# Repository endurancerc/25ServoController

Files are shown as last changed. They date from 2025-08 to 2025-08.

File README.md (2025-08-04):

# 25 Servo Controller

Build your own 25 Servo Controller! Once you have your circuit you must flash the bootloader firmware to your 
  device. Upload device firmware using the PICDEM tool.
  
The commercial version can be found here:

[http://www.endurance-rc.com/controllers.php#tfservo](http://www.endurance-rc.com/controllers.php#tfservo)

Requires Device Circuit.

-------------------------------------------------------------------------------------------------------------------------

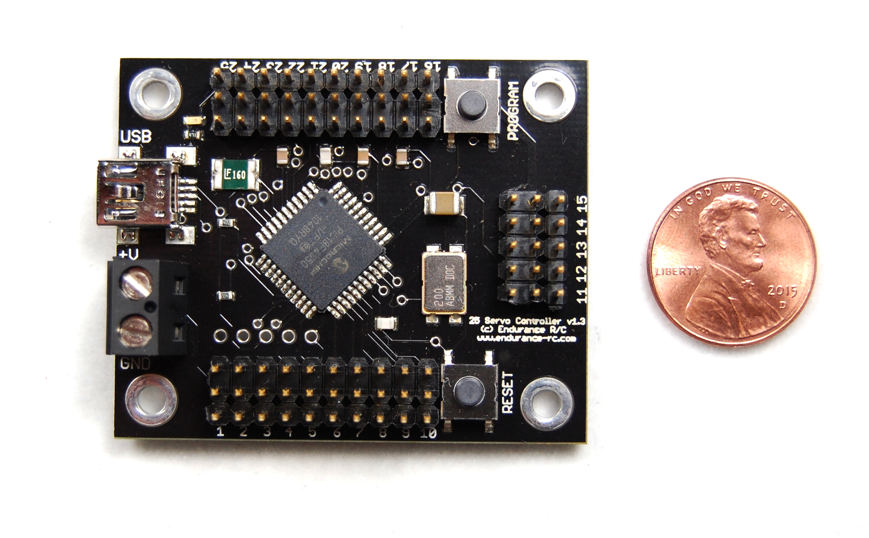
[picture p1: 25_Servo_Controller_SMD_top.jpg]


[25 Servo Controller Bill of Materials](https://github.com/endurancerc/PIC18F4550-25ServoController/blob/main/25_Servo_Controller_BOM.csv)

[25 Servo Controller Instructions](https://github.com/endurancerc/PIC18F4550-25ServoController/blob/main/25_servo_controller_v1.2_instructions.pdf)

-------------------------------------------------------------------------------------------------------------------------
        ______          __                                    ____     ________
       / ____/___  ____/ /_  ___________ _____  ________     / __ \  _/_/ ____/
      / __/ / __ \/ __  / / / / ___/ __ `/ __ \/ ___/ _ \   / /_/ /_/_// /     
     / /___/ / / / /_/ / /_/ / /  / /_/ / / / / /__/  __/  / _, _//_/ / /___   
    /_____/_/ /_/\__,_/\__,_/_/   \__,_/_/ /_/\___/\___/  /_/ /_/_/   \____/   

-------------------------------------------------------------------------------------------------------------------------

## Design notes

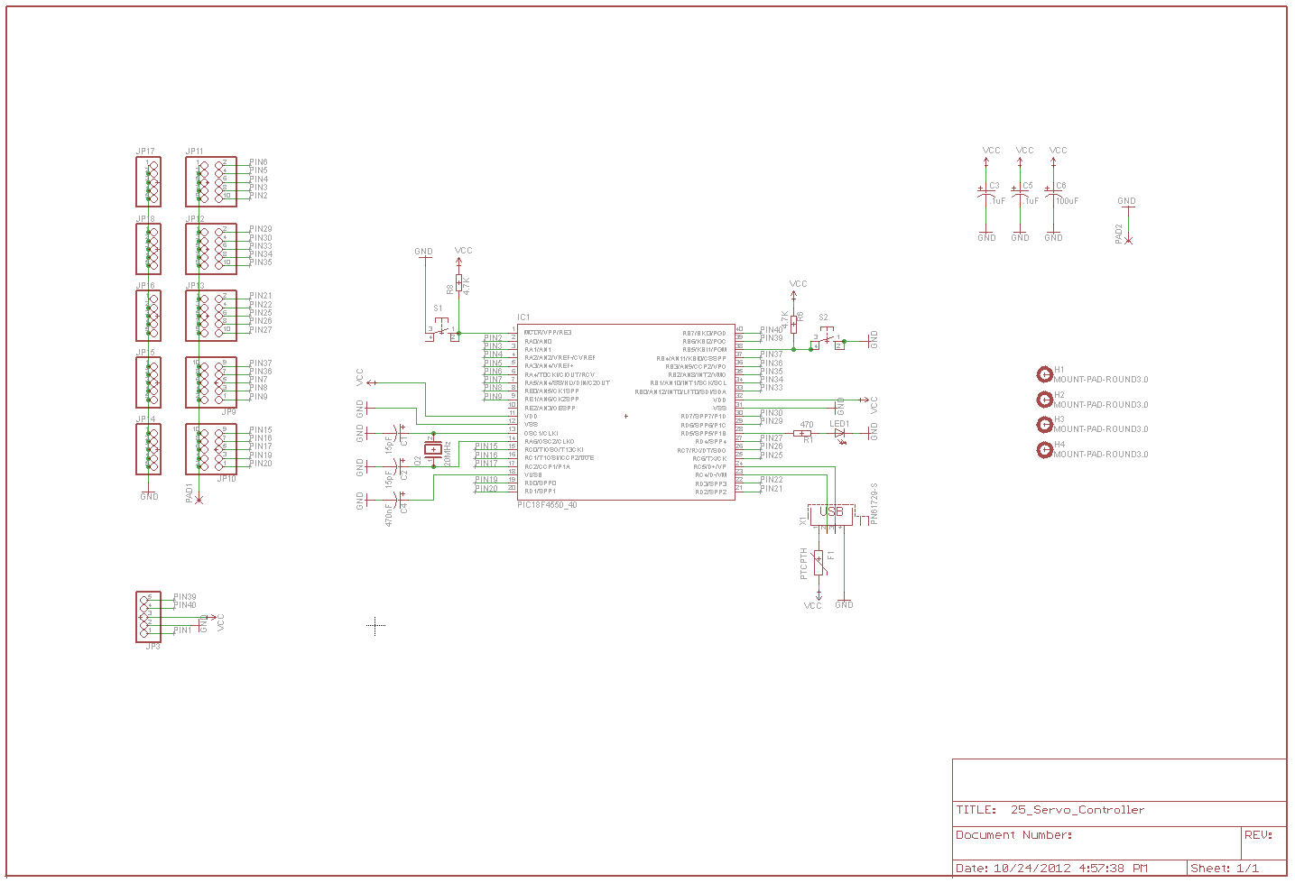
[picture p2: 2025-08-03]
Circuit_Board/25_Servo_Controller_Schematic.jpg

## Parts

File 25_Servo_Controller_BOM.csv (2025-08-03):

25 Servo Controller Parts Listing
Schematic Part ID | Mouser Part Number | Manufacturer Part Number | Description
IC1 | 579-PIC18F4550-I/P | PIC18F4550-I/P | Microcontrollers (MCU) 32kBF 2048RM FSUSB2
IC1 | 517-4840-6000-CP | 4840-6000-CP | IC & Component Sockets 40P DUAL WIPE DIPSKT
R6 | 291-4.7K-RC | 291-4.7K-RC | Carbon Film Resistors - Through Hole 4.7Kohms 0.05
R8 | 291-4.7K-RC | 291-4.7K-RC | Carbon Film Resistors - Through Hole 4.7Kohms 0.05
S1 | 653-B3F-1000 | B3F-1000 | Tactile & Jog Switches 6X6 FLAT 4.3mm BTN
S2 | 653-B3F-1000 | B3F-1000 | Tactile & Jog Switches 6X6 FLAT 4.3mm BTN
F1 | 576-30R160UPR | 30R160UPR | PTC Resettable Fuses 30V RADIAL LDS 1.60A RADIAL LEADS
Q2 | 815-ABL-20-B2 | ABL-20.000MHZ-B2 | Crystals +/-20ppm 20MHZ FUNDAMENTAL
C1 | 581-SR211A150KAR | SR211A150KAR | Multilayer Ceramic Capacitors (MLCC) - Leaded 100volts 15pF 10% C0G
C2 | 581-SR211A150KAR | SR211A150KAR | Multilayer Ceramic Capacitors (MLCC) - Leaded 100volts 15pF 10% C0G
C3 | 80-C410C104M5U | C410C104M5U5TA | Multilayer Ceramic Capacitors (MLCC) - Leaded 50volts .1uF 20%
C5 | 80-C410C104M5U | C410C104M5U5TA | Multilayer Ceramic Capacitors (MLCC) - Leaded 50volts .1uF 20%
C6 | 647-UVR1J101MPD1TD | UVR1J101MPD1TD | Aluminum Electrolytic Capacitors - Leaded 63volts 100uF
C4 | 140-SEA0R47M1HBK0407 | SEA0R47M1HBK-0407P | Aluminum Electrolytic Capacitors - Leaded 50V 0.47uF 20% 4X7mm
R1 | 660-MF1/4DC4700F | MF1/4DC4700F | Metal Film Resistors - Through Hole 470ohm 1% 100PPM
X1 | 571-292304-1 | 292304-1 | USB Connectors 4P 'B' RECEPTACLE
LED1 | 604-WP7113QBC/D | WP7113QBC/D | Standard LED - Through Hole BLUE WATER CLEAR
JP9-JP13 | 517-2350-6121TG | 2350-6121TG | Headers & Wire Housings 5P STRT 2 ROW GOLD
JP14-JP18 | 517-6111TG | 2340-6111TG | Headers & Wire Housings 5P STRT 1 ROW GOLD
PAD1/PAD2 | 538-39880-0302 | 39880-0302 | Fixed Terminal Blocks 2 CKT TERM. BLOCK 5.08mm
JP3 |  |  | ICSP: 1 - MCLR 2 - GND 3 - +5V 4 - PGD 5 - PGC

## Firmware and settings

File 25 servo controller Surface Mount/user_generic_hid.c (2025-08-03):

/** I N C L U D E S **********************************************************/
#include <p18cxxx.h>
#include <usart.h>
#include <delays.h>
#include "typedefs.h"
#include "usb.h"
#include "io_cfg.h"             // I/O pin mapping
#include "user_generic_hid.h"

/** V A R I A B L E S ********************************************************/
#pragma udata

byte number_of_bytes_read;
char transmit_buffer[EP0_BUFF_SIZE];
char receive_buffer[EP0_BUFF_SIZE];

int count;
unsigned int pulse1, pulse2, pulse3, pulse4, pulse5, pulse6, pulse7, pulse8;
unsigned int pulse9, pulse10, pulse11, pulse12, pulse13, pulse14, pulse15, pulse16;
unsigned int pulse17, pulse18, pulse19, pulse20, pulse21, pulse22, pulse23, pulse24, pulse25;

unsigned int dif1, dif2, dif3, dif4, dif5, dif6, dif7, dif8;
unsigned int dif9, dif10, dif11, dif12, dif13;

/** P R I V A T E  P R O T O T Y P E S ***************************************/
void BlinkUSBStatus(void);
void ReportLoopback(void);
void HandleControlOutReport(void);
void step(int);

/** D E C L A R A T I O N S **************************************************/
#pragma code
void UserInit(void) {

	//PWM Pins
	TRISDbits.TRISD2 = 0; //pin d2 output, output 1
	TRISDbits.TRISD3 = 0; //pin d3 output, output 2
	TRISCbits.TRISC6 = 0; //pin c6 output, output 3
	//TRISCbits.TRISC7 = 0; //pin c7 output, output 4
	TRISDbits.TRISD4 = 0; //pin d4 output, output 5
	TRISDbits.TRISD6 = 0; //pin d6 output, output 6
	TRISDbits.TRISD7 = 0; //pin d7 output, output 7
	TRISBbits.TRISB0 = 0; //pin b0 output, output 8
	TRISBbits.TRISB1 = 0; //pin b1 output, output 9
	TRISBbits.TRISB2 = 0; //pin b2 output, output 10
	TRISAbits.TRISA4 = 0; //pin a4 output, output 11
	TRISAbits.TRISA3 = 0; //pin a3 output, output 12
	TRISAbits.TRISA2 = 0; //pin a2 output, output 13
	TRISAbits.TRISA1 = 0; //pin a1 output, output 14
	TRISAbits.TRISA0 = 0; //pin a0 output, output 15
	TRISBbits.TRISB4 = 0; //pin b4 output, output 16
	TRISBbits.TRISB3 = 0; //pin b3 output, output 17
	TRISAbits.TRISA5 = 0; //pin a5 output, output 18
	TRISEbits.TRISE0 = 0; //pin e0 output, output 19
	TRISEbits.TRISE1 = 0; //pin e1 output, output 20
	TRISCbits.TRISC0 = 0; //pin c0 output, output 21
	TRISCbits.TRISC1 = 0; //pin c1 output, output 22
	TRISCbits.TRISC2 = 0; //pin c2 output, output 23
	TRISDbits.TRISD0 = 0; //pin d0 output, output 24
	TRISDbits.TRISD1 = 0; //pin d1 output, output 25

	//LED Pin
	TRISCbits.TRISC7 = 0; //pin C7 output
	LATCbits.LATC7 = 1; //on
	//TRISDbits.TRISD5 = 0; //pin d5 output
	//LATDbits.LATD5 = 1; //on

	// Timer2 prescale = 16
	T2CONbits.T2CKPS0 = 0;
	T2CONbits.T2CKPS1 = 1;
	
	// Timer2 postscale = 16
	T2CONbits.T2OUTPS0 = 1;
	T2CONbits.T2OUTPS1 = 1;
	T2CONbits.T2OUTPS2 = 1;
	T2CONbits.T2OUTPS3 = 1;

	// Timer period
	PR2 = 0xE9;  //233
	//83.3*16*16*(233+1)= 5ms

	// Timer2 is on
	T2CONbits.TMR2ON = 1;

    // Enable Timer2 interrupt
    PIE1bits.TMR2IE = 1;

	count = 2;
	pulse1 = 150;
	pulse2 = 150;
	pulse3 = 150;
	pulse4 = 150;
	pulse5 = 150;
	pulse6 = 150;
	pulse7 = 150;
	pulse8 = 150;
	pulse9 = 150;
	pulse10 = 150;
	pulse11 = 150;
	pulse12 = 150;
	pulse13 = 150;
	pulse14 = 150;
	pulse15 = 150;
	pulse16 = 150;
	pulse17 = 150;
	pulse18 = 150;
	pulse19 = 150;
	pulse20 = 150;
	pulse21 = 150;
	pulse22 = 150;
	pulse23 = 150;
	pulse24 = 150;
	pulse25 = 150;

	dif1 = 0;
	dif2 = 0;
	dif3 = 0;
	dif4 = 0;
	dif5 = 0;
	dif6 = 0;
	dif7 = 0;
	dif8 = 0;
	dif9 = 0;
	dif10 = 0;
	dif11 = 0;
	dif12 = 0;
	dif13 = 0;
}


void ProcessIO(void) {   
	unsigned int arr[3];
 	unsigned int sorted[3];
	int a, i;

    if((usb_device_state < CONFIGURED_STATE)||(UCONbits.SUSPND==1)) {
		return;
	}
    
	ReportLoopback();

    if (PIR1bits.TMR2IF) {
    	if (--count == 0) {
			T2CONbits.TMR2ON = 0; 	//turn off the timer
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
